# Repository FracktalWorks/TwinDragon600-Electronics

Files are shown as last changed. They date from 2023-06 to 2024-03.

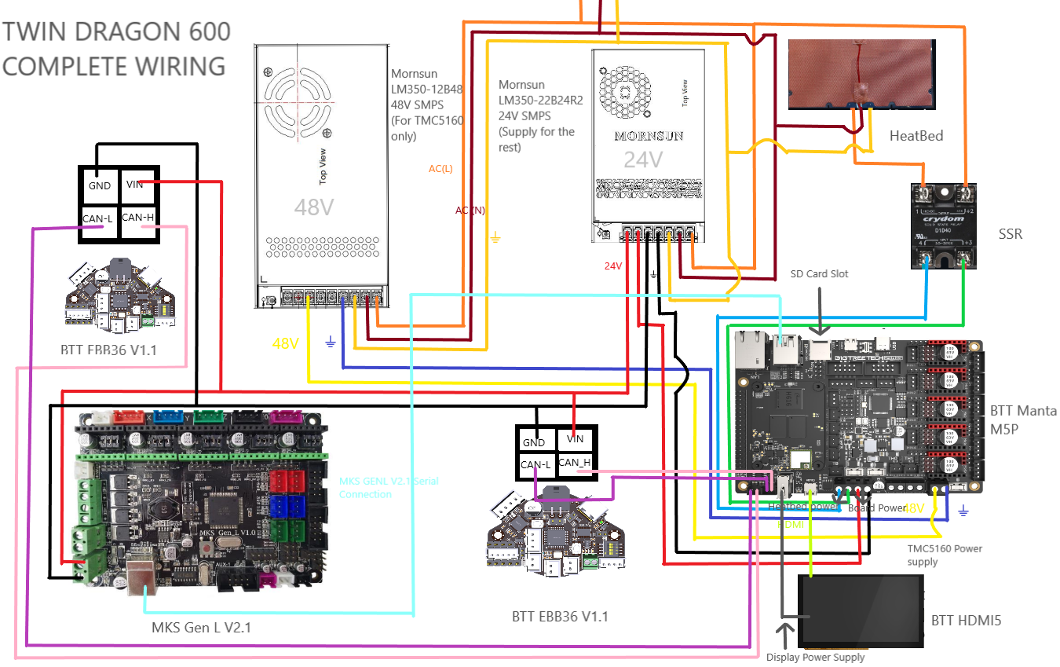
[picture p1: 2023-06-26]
Twin Dragon 600 Wiring.png

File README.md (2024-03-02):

# TwinDragon600-Electronics

### For the Combination of BTT Manta M5P + BTT CB1 + BTT EBB36 + MKS Gen L V2.1

Electronic description, pinout and manuals for the electronics used in Twin Dragon 600

Pin Configurations, jumper selection, CanBus and multi-MCU wiring to BTT CB1 embedded onto BTT Manta M5P for Twin Dragon 600

Components used:
1. BTT Manta M5P - 1
2. BTT CB1 (embed onto BTT Manta M5P) - 1
3. BTT EBB36 Can Module/Toolboard - 2
4. TMC5160 Stepper drivers - 5
5. MKS Gen L V2.1 - 1
6. TMC2209 stepper drivers - 2 (On the MKS GenL) + 2 (Present on the BTT EBB36's)
7. BTT HDMI5 Touch Display

### For the Combination of BTT Manta M8P + BTT CB1 + RP2040 based toolboard

Pin Configurations, jumper selection, CanBus and multi-MCU wiring to BTT CB1 embedded onto BTT Manta M8P for Twin Dragon 600

Components used:
1. BTT Manta M8P - 1
2. BTT CB1 (embed onto BTT Manta M8P) - 1
3. RP2040 based Can Module/Toolboard - 2
4. TMC5160 Stepper drivers - 5
5. TMC2209 stepper drivers - 2 (On the MKS GenL) + 2 (Present on the Toolboards)
6. BTT HDMI5 Touch Display

## Setting up BTT Manta M5P + BTT CB1 + BTT EBB36 + MKS Gen L V2.1

### Initial Preparation

At the Initial stage, when needed to only access the CB1 module with USB power supply, a jumper is to be placed in the slot mentioned as 'VUSB' present between the micro HDMI port and the SOC-SD card slot.


This should not be inserted when the board is supplied with 24V and fully functioning.

### Other Initial preparation and setting up jumpers

#### TMC Driver SPI Mode


The first row are the defined pin for the drivers, which are either high or low when shorted or unshorted to establish different mode of communication. The second row are defined with the SPI modes, with the namings of 'MISO', 'CS', 'SCK' and 'MOSI' when read from left to right. Since we use the TMC5160 driver, it specifically operates only on the SPI mode. Insert the jumpers corresponding to its parallel pins only on the 1st and the 2nd row as shown in the image.

#### Driver Voltage selection


Since the TMC5160 operates only on SPI mode, which is specifically for achieving faster communication and higher speeds, it needs an operating voltage of around 48V. The manta M5P has seperte pins for regular voltage of 24V and high voltage of 48V, that is to be jumped to the common pin of voltage supply to the drivers. We jump the HV pin in the left to the middle pin of supply in order to provide 48V to the drivers, as shown in the image above.

#### Setting up jumper for probe activation


The pin for probe used here is the IND-probe pin on Manta M5P, and the jumper is placed on the two pins beside the probe pins as shown in the image above, to enable 24V supply to the ABL board.

#### Setting up Jumper for CANBUS communication


At the bottom-left corner of the board, a small jumper is to be placed on the pins that mention '120R' depicting the 120 ohms resistance that is applied on the CAN Low and High communication pins. This is a crucial pin for the setting up of the CAN communication of the motherboard and toolboard.

## Setting up of BTT EBB36 CAN module/Toolboard

### Initial preparation


After the motherboard is powered on, the yellow-green LED1 lights will light up, indicating a normal power supply. The VUSB on the right side of the board is the power selection terminal. Only when using USB to supply power to the motherboard or need to supply power through USB, do you need to use the jumper cap to connect VUSB.

#### Setting up Jumper for CANBUS communication


Similar to the BTT Manta M5P, the Support communication via CAN or USB. The terminal resistor 120R of CAN can be selected through a jumper cap, and it reserves a CAN expansion interface.

#### Placing of Heatsink


Place the Heatsink onto the TMC2209 driver chip present on the board which is already embedded onto it as shown in the image above.

## Setting up of MKS GenL V2.1 for side extruder motors

### Setting up jumpers for enabling UART mode


Since we use the TMC2209 for the side extruder motors similar to the main extruder motors, we set the drivers in UART mode

## Wiring and Connections
Twin Dragon 600 Wiring

The overall connections of all the Electrical and Electronic components are present in the image above

### BTT Manta M5P Pin connections
BTT manta M5P pin connections

### EBB36 Pin connections
EBB36 pin connections



The setting up of CANBUS communication in the right angle to avoid confusion

### MKS GenL V2.1 Pin Conections


In the above image, the pin connections of side extruder motors are given, along with additional ports for the extruder filament sensors

## Setting up BTT Manta M8P + BTT CB1 + RP2040 based toolboard

### Initial Preparation

At the Initial stage, when needed to only access the CB1 module with USB power supply, a jumper is to be placed in the slot mentioned as 'VUSB' present behind the Type-C port. After the M8P motherboard is powered on, the D32 red light on the left side of the MCU will light up, indicating that the power supply is normal.



### Other Initial preparation and setting up jumpers

#### TMC Driver SPI Mode



The first row are the defined pin for the drivers, which are either high or low when shorted or unshorted to establish different mode of communication. The second row are defined with the SPI modes, with the namings of 'MISO', 'CS', 'SCK' and 'MOSI' when read from left to right. Since we use the TMC5160 driver, it specifically operates only on the SPI mode. Insert the jumpers corresponding to its parallel pins only on the 1st and the 2nd row as shown in the image.

#### TMC Driver UART Mode



The given set of pin to short is the CS pin that enables only the uart mode.

#### Driver Voltage selection

For High Voltage selection(48V):



Since the TMC5160 operates only on SPI mode, which is specifically for achieving faster communication and higher speeds, it needs an operating voltage of around 48V. The manta M8P has seperte pins for regular voltage of 24V and high voltage of 48V, that is to be jumped to the common pin of voltage supply to the drivers. We jump the HV pin in the left to the middle pin of supply in order to provide 48V to the drivers, as shown in the image above.

For normal Voltage selection (24V):



This voltage selection can be used when using a regular TMC2209 on the UART mode

#### Setting up jumper for probe activation



The pin for probe used here is the IND-probe pin on Manta M8P, and the jumper is placed on the two pins beside the probe pins as shown in the image above, to enable 24V supply to the ABL board.

#### Setting up Jumper for CANBUS communication



At the top of the two CAN pins, a small jumper is to be placed on the pins that mention '120R' depicting the 120 ohms resistance that is applied on the CAN Low and High communication pins. This is a crucial pin for the setting up of the CAN communication of the motherboard and toolboard.

## Setting up of RP2040 based CAN module/Toolboard



After the motherboard is powered on, the green LED light will light up, indicating a normal power supply. The VBUS on the right side of the board is the power selection terminal. Only when using USB to supply power to the motherboard or need to supply power through USB, do you need to use the jumper cap to connect VBUS.

Similar to the BTT Manta M8P, the Support communication via CAN or USB. The terminal resistor 120R of CAN can be selected through a jumper cap, and it reserves a CAN expansion interface.

## Wiring and Connections

Twin Dragon 600 with M8P Wiring

The overall connections of all the Electrical and Electronic components are present in the image above

  ### BTT Manta M8P Pin connections



## Setting up BTT Manta M8P V2.0 + RPi CM4 + RP2040 based toolboard

After powering on the M8P, the LED on the bottom left corner will light up to indicate normal power supply. The VUSB jumper in the center is for selecting power - it should only be shorted when powering the board via USB or supplying power out via USB.



### Other Initial preparation and setting up jumpers

#### TMC Driver SPI Mode



The first row are the defined pin for the drivers, which are either high or low when shorted or unshorted to establish different mode of communication. The second row are defined with the SPI modes, with the namings of 'MISO', 'CS', 'SCK' and 'MOSI' when read from left to right. Since we use the TMC5160 driver, it specifically operates only on the SPI mode. Insert the jumpers corresponding to its parallel pins only on the 1st and the 2nd row as shown in the image.

#### TMC Driver UART Mode



The given set of pin to short is the CS pin that enables only the uart mode.

#### Driver Voltage selection

For High Voltage selection(48V):



Since the TMC5160 operates only on SPI mode, which is specifically for achieving faster communication and higher speeds, it needs an operating voltage of around 48V. The manta M8P has seperte pins for regular voltage of 24V and high voltage of 48V, that is to be jumped to the common pin of voltage supply to the drivers. We jump the HV pin in the left to the middle pin of supply in order to provide 48V to the drivers, as shown in the image above.

For normal Voltage selection (24V):



This voltage selection can be used when using a regular TMC2209 on the UART mode

#### Setting up jumper for probe activation



The pin for probe used here is the IND-probe pin on Manta M8P V2.0, and the jumpers are placed on the two pins beside the probe pins, and other three perpendicular pins to its right, where the top two are to jumped together to activate the probe pin, as shown in the image above, to enable 24V/5V supply to the ABL board. The three columns of the pins starting from the top are 5V, 12V, 24V Respectively.

#### Setting up Jumper for CANBUS communication



At the left of the CAN pin, a small jumper is to be placed on the pins that mention '120R' depicting the 120 ohms resistance that is applied on the CAN Low and High communication pins. This is a crucial pin for the setting up of the CAN communication of the motherboard and toolboard.

## Wiring and Connections

Twin Dragon 600 CM4 M8P V2 0 - Wiring

The overall connections of all the Electrical and Electronic components are present in the image above

### BTT Manta M8P V2.0 Pin connections

Twin Dragon 600 with M8P V2 0 Wiring

## To setup Raspeberry Pi camera Rev 1.3, interfaced with RPi CM4 and BTT Manta M8P/M5P

In order to interface the Pi camera Rev 1.3 with the RPi CM4 and BTT Manta M8P/M5P, flip the board and check for a CSI1 camera slot, which should look like the image below



Instructions to attach the camera in BTT Manta M8P V2.0



Instructions to attach the camera in BTT Manta M5P

1. Now, boot up the board (including CM4), SSH into the CM4 and open the terminal
2. We will have to download a bin file into the boot folder of the CM4, below is the command to enter into the terminal.

`sudo wget https://datasheets.raspberrypi.com/cmio/dt-blob-cam1.bin -O /boot/dt-blob.bin`

If the above command does not work, try the following command:

`sudo wget https://datasheets.raspberrypi.com/cmio/dt-blob-cam1.bin -O /boot/firmware/dt-blob.bin`

3. Now, in the terminal, enter `sudo raspi-config` and select the option '3 Interface Options    Configure connections to peripherals'. Now select the first option 'P1 Camera      Enable/disable connection to the Raspberry Pi Camera'. A pop-up would appear where it asks to enable the camera. Make sure to select <yes> and exit the portal.

4. Now, in the terminal, type in `sudo nano /boot/config.txt` and make sure the settings are enabled

   `start_x=1
   gpu_mem=128`

   Note: make sure `#camera_auto_select=1` is commented out, or else it will not work.

For more clarifications, check out 'Julia TouchUI documentation' for more settings on Pi-camera

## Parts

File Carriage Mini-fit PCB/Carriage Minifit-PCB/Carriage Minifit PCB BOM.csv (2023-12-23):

Qty | Designator | Footprint | Comment | LCSC Part # | Description | Value
1 | J1 | MOLEX_39281063 | 39281063 |  | Conn Wire to Board HDR 6Power POS 4.2mm Solder ST Top Entry Thru-Hole Mini-Fit Jr Bag Check availability | 39281063
1 | X1 | JST-XH-02-PACKAGE-LONG-PAD | JST-XH-02-PIN-LONG-PAD |  | JST XH Connector 2 Pin | JST-XH-02-PIN-LONG-PAD
1 | X2 | TERMINAL-BLOCK-4-PIN-3.5MM-LONG-PAD | TERMINAL-BLOCK-3.5MM-4-PIN-LONG-PAD |  | Terminal Block 3.5mm | TERMINAL-BLOCK-3.5MM-4-PIN-LONG-PAD

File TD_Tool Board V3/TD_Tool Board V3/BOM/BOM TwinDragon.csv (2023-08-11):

Qty | Designator | Footprint | Comment | LCSC part# | Description | Value
1 | J1 | SCREWTERMINAL-3.5MM-2 | CONN_023.5MM |  | Multi connection point. Often used as Generic Header-pin footprint for 0.1 inch spaced/style header connections
2 | R8, R14 | RESC1005X40 | R_CHIP-0402(1005-METRIC) | C25741 | Resistor Fixed - Generic | 100k
22 | C5, C6, C7, C8, C9, C10, C11, C12, C16, C17, C18, C20, C24, C25, C26, C27, C29, C30, C31, C34, C39, C40 | CAPC1005X60 | C_CHIP-0402(1005-METRIC) | C307331 | Capacitor - Generic | 100nF
1 | C33 | PANASONIC_D | 100UF-POLAR-25V-20%(ELEC) | C128464 | 100µF polarized capacitors | 100uF
1 | R6 | RESC1005X40 | R_CHIP-0402(1005-METRIC) | C2933067 | Resistor Fixed - Generic | 105k
4 | R21, R22, R37, R41 | RESC1005X40 | R_CHIP-0402(1005-METRIC) | C25744 | Resistor Fixed - Generic | 10K
1 | C19 | CAPC1608X85 | C_CHIP-0603(1608-METRIC) | C194427 | Capacitor - Generic | 10uF
1 | R16 | RESC1005X40 | R_CHIP-0402(1005-METRIC) | C25079 | Resistor Fixed - Generic | 120R
1 | R9 | RESC1005X40 | R_CHIP-0402(1005-METRIC) | C2974007 | Resistor Fixed - Generic | 13.3k
6 | R3, R12, R23, R24, R25, R40 | RESC1005X40 | R_CHIP-0402(1005-METRIC) | C25543 | Resistor Fixed - Generic | 1K
1 | R2 | RESC1005X40 | R_CHIP-0402(1005-METRIC) | C25086 | Resistor Fixed - Generic | 1R
5 | C3, C4, C13, C14, C15 | CAPC1005X60 | C_CHIP-0402(1005-METRIC) | C52923 | Capacitor - Generic | 1uF
2 | R35, R36 | RESC1005X40 | R_CHIP-0402(1005-METRIC) | C425373 | Resistor Fixed - Generic | 2.37K
1 | R1 | RESC1005X40 | R_CHIP-0402(1005-METRIC) | C25087 | Resistor Fixed - Generic | 200R
4 | R30, R45, R47, R49 | RESC1005X40 | R_CHIP-0402(1005-METRIC) | C25765 | Resistor Fixed - Generic | 20K
2 | R26, R27 | RESC1005X40 | R_CHIP-0402(1005-METRIC) | C705474 | Resistor Fixed - Generic | 220mΩ
1 | C28 | CAPC1005X60 | C_CHIP-0402(1005-METRIC) | C1532 | Capacitor - Generic | 22nF
3 | C21, C22, C38 | CAPC2012X110 | C_CHIP-0805(2012-METRIC) | C338080 | Capacitor - Generic | 22uF
6 | R10, R11, R31, R44, R46, R48 | RESC1005X40 | R_CHIP-0402(1005-METRIC) | C31439 | Resistor Fixed - Generic | 27.4R
1 | P2 | SOT23-5 | V_REG_AP2112K-3.3V | C51118 | AP2112 - 600mA CMOS LDO Regulator w/ Enable | 3.3V
2 | C1, C2 | CAPC1005X60 | C_CHIP-0402(1005-METRIC) | C1570 | Capacitor - Generic | 30pF
1 | R34 | RESC1005X40 | R_CHIP-0402(1005-METRIC) | C227106 | Resistor Fixed - Generic | 4.12K
5 | R17, R18, R19, R20, R33 | RESC1005X40 | R_CHIP-0402(1005-METRIC) | C304616 | Resistor Fixed - Generic | 4.7K
5 | C32, C42, C43, C44, C45 | CAPC1608X85 | C_CHIP-0603(1608-METRIC) | C162274 | Capacitor - Generic | 4.7uF
3 | R7, R15, R28 | RESC1005X40 | R_CHIP-0402(1005-METRIC) | C25120 | Resistor Fixed - Generic | 49.9R
1 | R5 | RESC1005X40 | R_CHIP-0402(1005-METRIC) | C3037035 | Resistor Fixed - Generic | 511k
1 | C23 | CAPC1005X60 | C_CHIP-0402(1005-METRIC) | C37809 | Capacitor - Generic | 75pF
1 | L2 | ACM2012_TDK | ACM2012-201-2P-T002ACM2012_TDK | C3029258 |  | ACM2012
1 | U5 | ADXL345_LGA14 | ADXL345BCCZ-RL | C9667 | Digital Accelerometer | ADXL345
1 | L1 | SMDRI74-680MT | ASPI-0630HI-100M-T157X7X4 | C3000391 | Inductor Power Molded Wirewound 10uH 20% 3A 105mOhm DCR T/R | ASPI-0630HI-100M-T157X7X4
2 | BOOT, RST | B3U-1000P(M)-B | B3U-X000B3U-1000P(M)-B1000P(M)-B | C231329 | Ultra-small Tactile Switch | B3U-1000P(M)-B
4 | D4, D6, D7, D8 | SOT23 | BAT54S | C47546 |  | BAT54S
3 | M2, M3, M4 | SOT23 | NMOSFET_BSS123_SOT23-GSD | C19019 | N-Channel MOSFET - Popular parts | CJ3400
1 | X1 | CRYSTAL_3225 | CRYSTAL_TAXM12M4RLBDDT2T_3225 | C133334 |  | CRYSTAL_TAXM12M4RLBDDT2T_3225
1 | R13 | RESC1005X40 | R_CHIP-0402(1005-METRIC) | NO-FIT | Resistor Fixed - Generic | DO NOT FIT (10K)
3 | FD4, FD5, FD6 | FIDUCIAL_1MM | FIDUCIAL |  | For use by pick and place machines to calibrate the vision/machine, 1mm | FIDUCIAL
1 | F1 | FUSC1608X60N | FUSE_CHIP-0603(1608-METRIC) | C261937 | Fuse - Generic | FUSE_CHIP-0603(1608-METRIC)
1 | J3 | CON_430450400_MOL | 430450400CON_430450400_MOL |  |  | JST-MICROFIT
1 | C_FAN2 | JST-XH-02-PACKAGE-LONG-PAD | JST-XH-02-PIN-LONG-PAD |  | JST XH Connector 2 Pin | JST-XH
5 | CANBUS, C_FAN, ENDSTOP, H_FAN, M_FAN | JST-XH-02-PACKAGE-LONG-PAD | JST-XH-02-PIN-LONG-PAD |  | JST XH Connector 2 Pin | JST-XH-02-PIN-LONG-PAD
1 | EXTRUDER | JST-XH-04-PACKAGE-LONG-PAD | JST-XH-04-PIN-LONG-PAD |  | JST XH Connector 2 Pin | JST-XH-04-PIN-LONG-PAD
1 | D3 | LEDC1608X35N_FLAT-G | CHIP-FLAT-G_0603-0.35MM | C72043 |  | LED_G
1 | D9 | LED3MM | LED3MM | C72043 | LED | LED_G
1 | D1 | SODFL3718X115 | SCHOTTKY_MBR0520LT1GDO-219 | C23848 | Schottky Diode - Popular parts | MBR0520LT1G
1 | M1 | NMOSFET_WSD3066DN33 | NMOSFET_WSD3066DN33 | C148386 |  | NMOSFET_WSD3066DN33
1 | R4 | RESC1005X40 | R_CHIP-0402(1005-METRIC) | NO-FIT | Resistor Fixed - Generic | NO-FIT
1 | U1 | IC57_RP2040-L | RP2040IC57_RP2040-L | C2040 |  | RP2040
1 | U3 | D8-L | SN65HVD1050DRD8-L | C14019 |  | SN65HVD
1 | U6 | DBV5-L | SN74LVC1G17DBVRDBV5-L | C7836 |  | SN74L
1 | SJ2 | SJ_2S-NO | SOLDERJUMPERNO |  | Solder Jumper | SOLDERJUMPERNO
2 | SJ1, SJ3 | SJ_2S-TRACE | SOLDERJUMPERTRACE |  | Solder Jumper | SOLDERJUMPERTRACE
2 | IO1, IO2 | PAD.03X.03 | TEST-POINT3 |  | SparkFun Test Points | TEST-POINT3
10 | 3.3V, 5V, 24V, A1, A2, B1, B2, GND, HE0, TH0 | PAD.03X.04 | TEST-POINT3X4 |  | SparkFun Test Points | TEST-POINT3X4
1 | U7 | QFN28_5X5_3X8_EPAD_TRI | TMC2209-LA-TQFN28_5X5_3X8_EPAD_TRI | C2150710 |  | TMC2209
1 | P1 | SOT-23-6 | TPS54202_BUCKCONV | C191884 |  | TPS54202_BUCKCONV
1 | USB | CONN12_016JA1R1500_JAE | USB-C(DX07S016JA1R1500) | C709357 |  | USB-C(DX07S016JA1R1500)
1 | D2 | SOT-666_STM-L | USBLC6-2P6SOT-666_STM-L | C2827693 |  | USBLC6-2P6SOT-666_STM-L
1 | U2 | SOIC_128JVSIQ_WIN-L | W25Q128JVSIQSOIC_128JVSIQ_WIN-L | C97521 |  | W25Q128

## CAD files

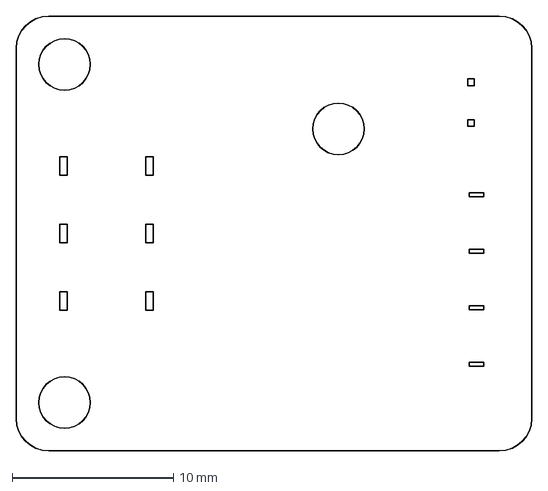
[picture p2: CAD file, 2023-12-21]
Carriage Mini-fit PCB/TD Carriage MINIFIT board.dxf
32.0 x 27.0 mm

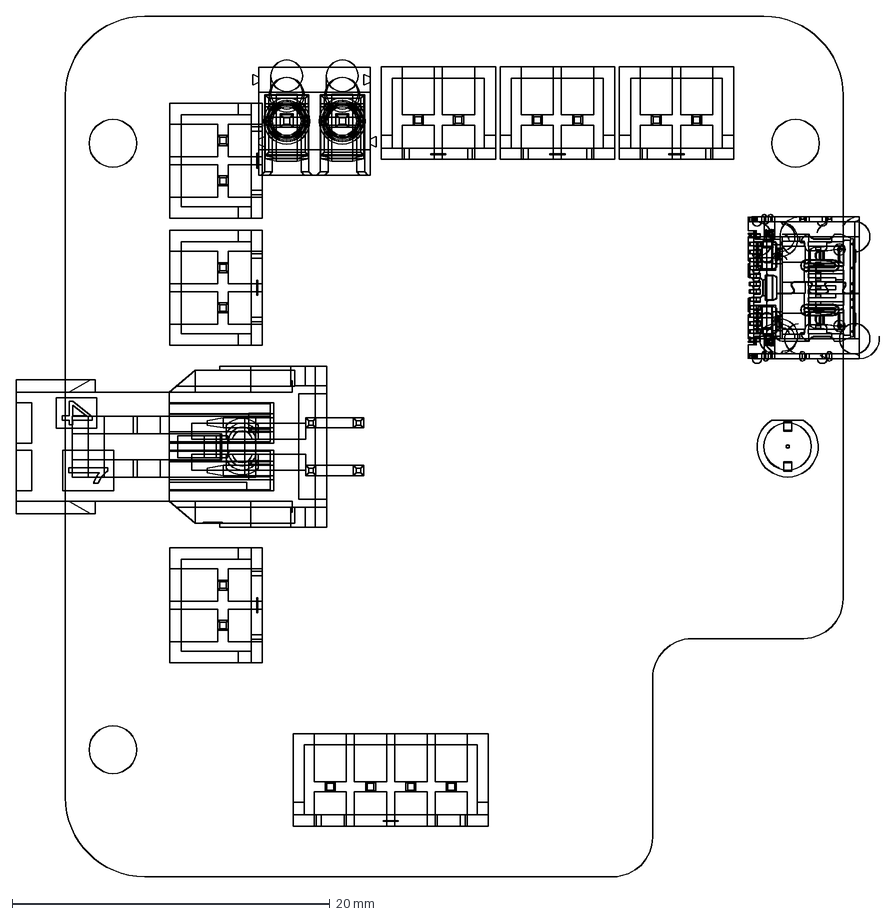
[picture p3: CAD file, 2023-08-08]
TD_Tool Board V3/PCB V2.1.dxf
54.4 x 54.2 mm

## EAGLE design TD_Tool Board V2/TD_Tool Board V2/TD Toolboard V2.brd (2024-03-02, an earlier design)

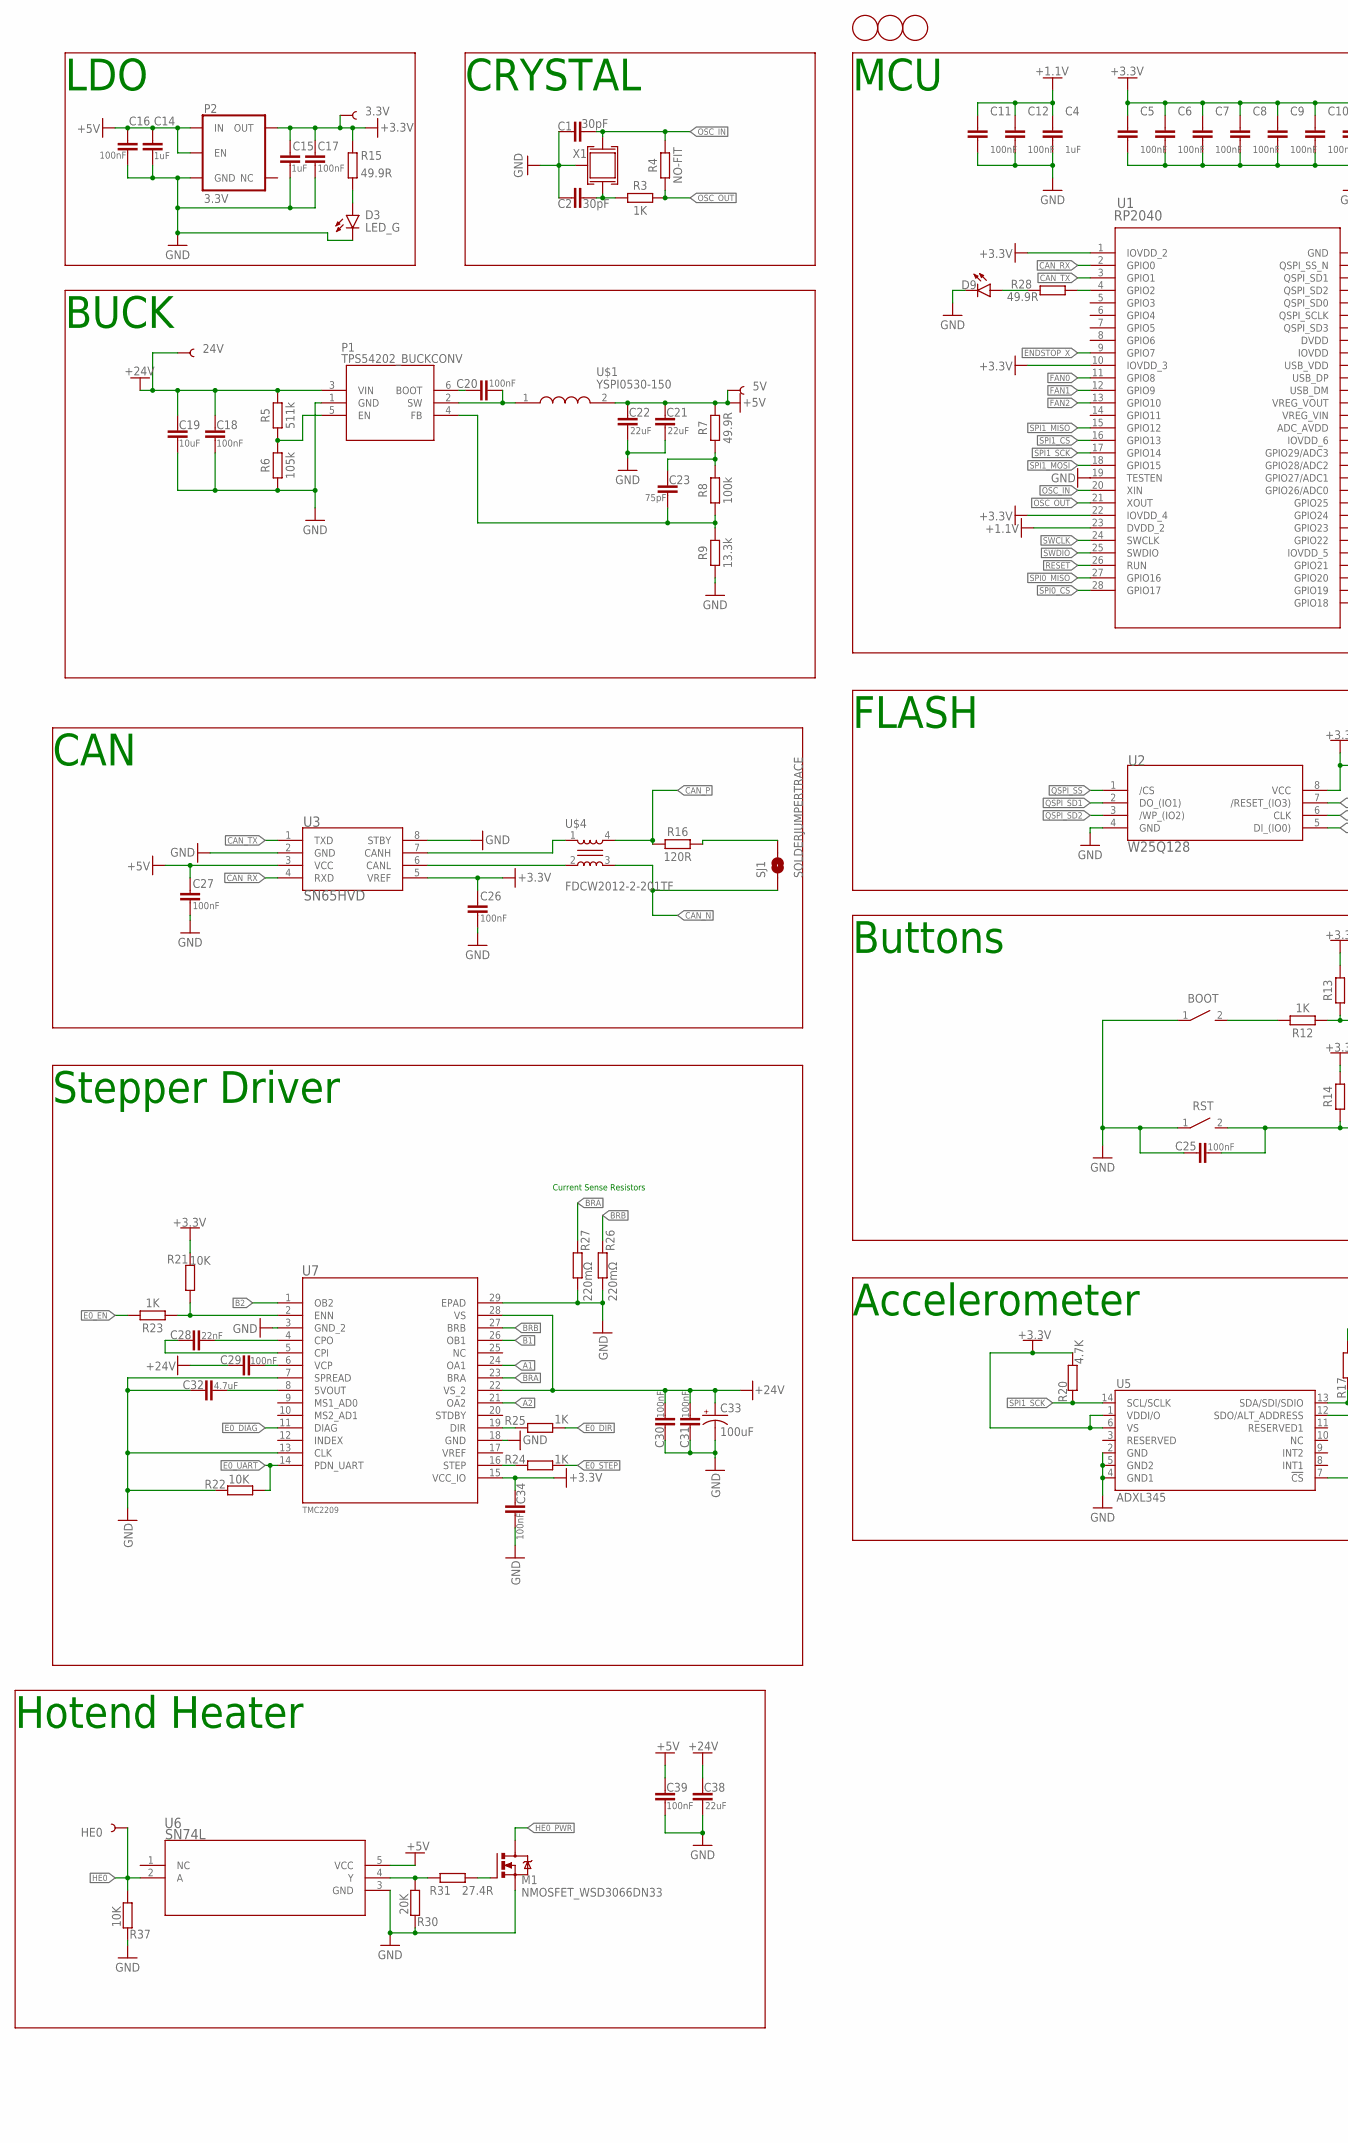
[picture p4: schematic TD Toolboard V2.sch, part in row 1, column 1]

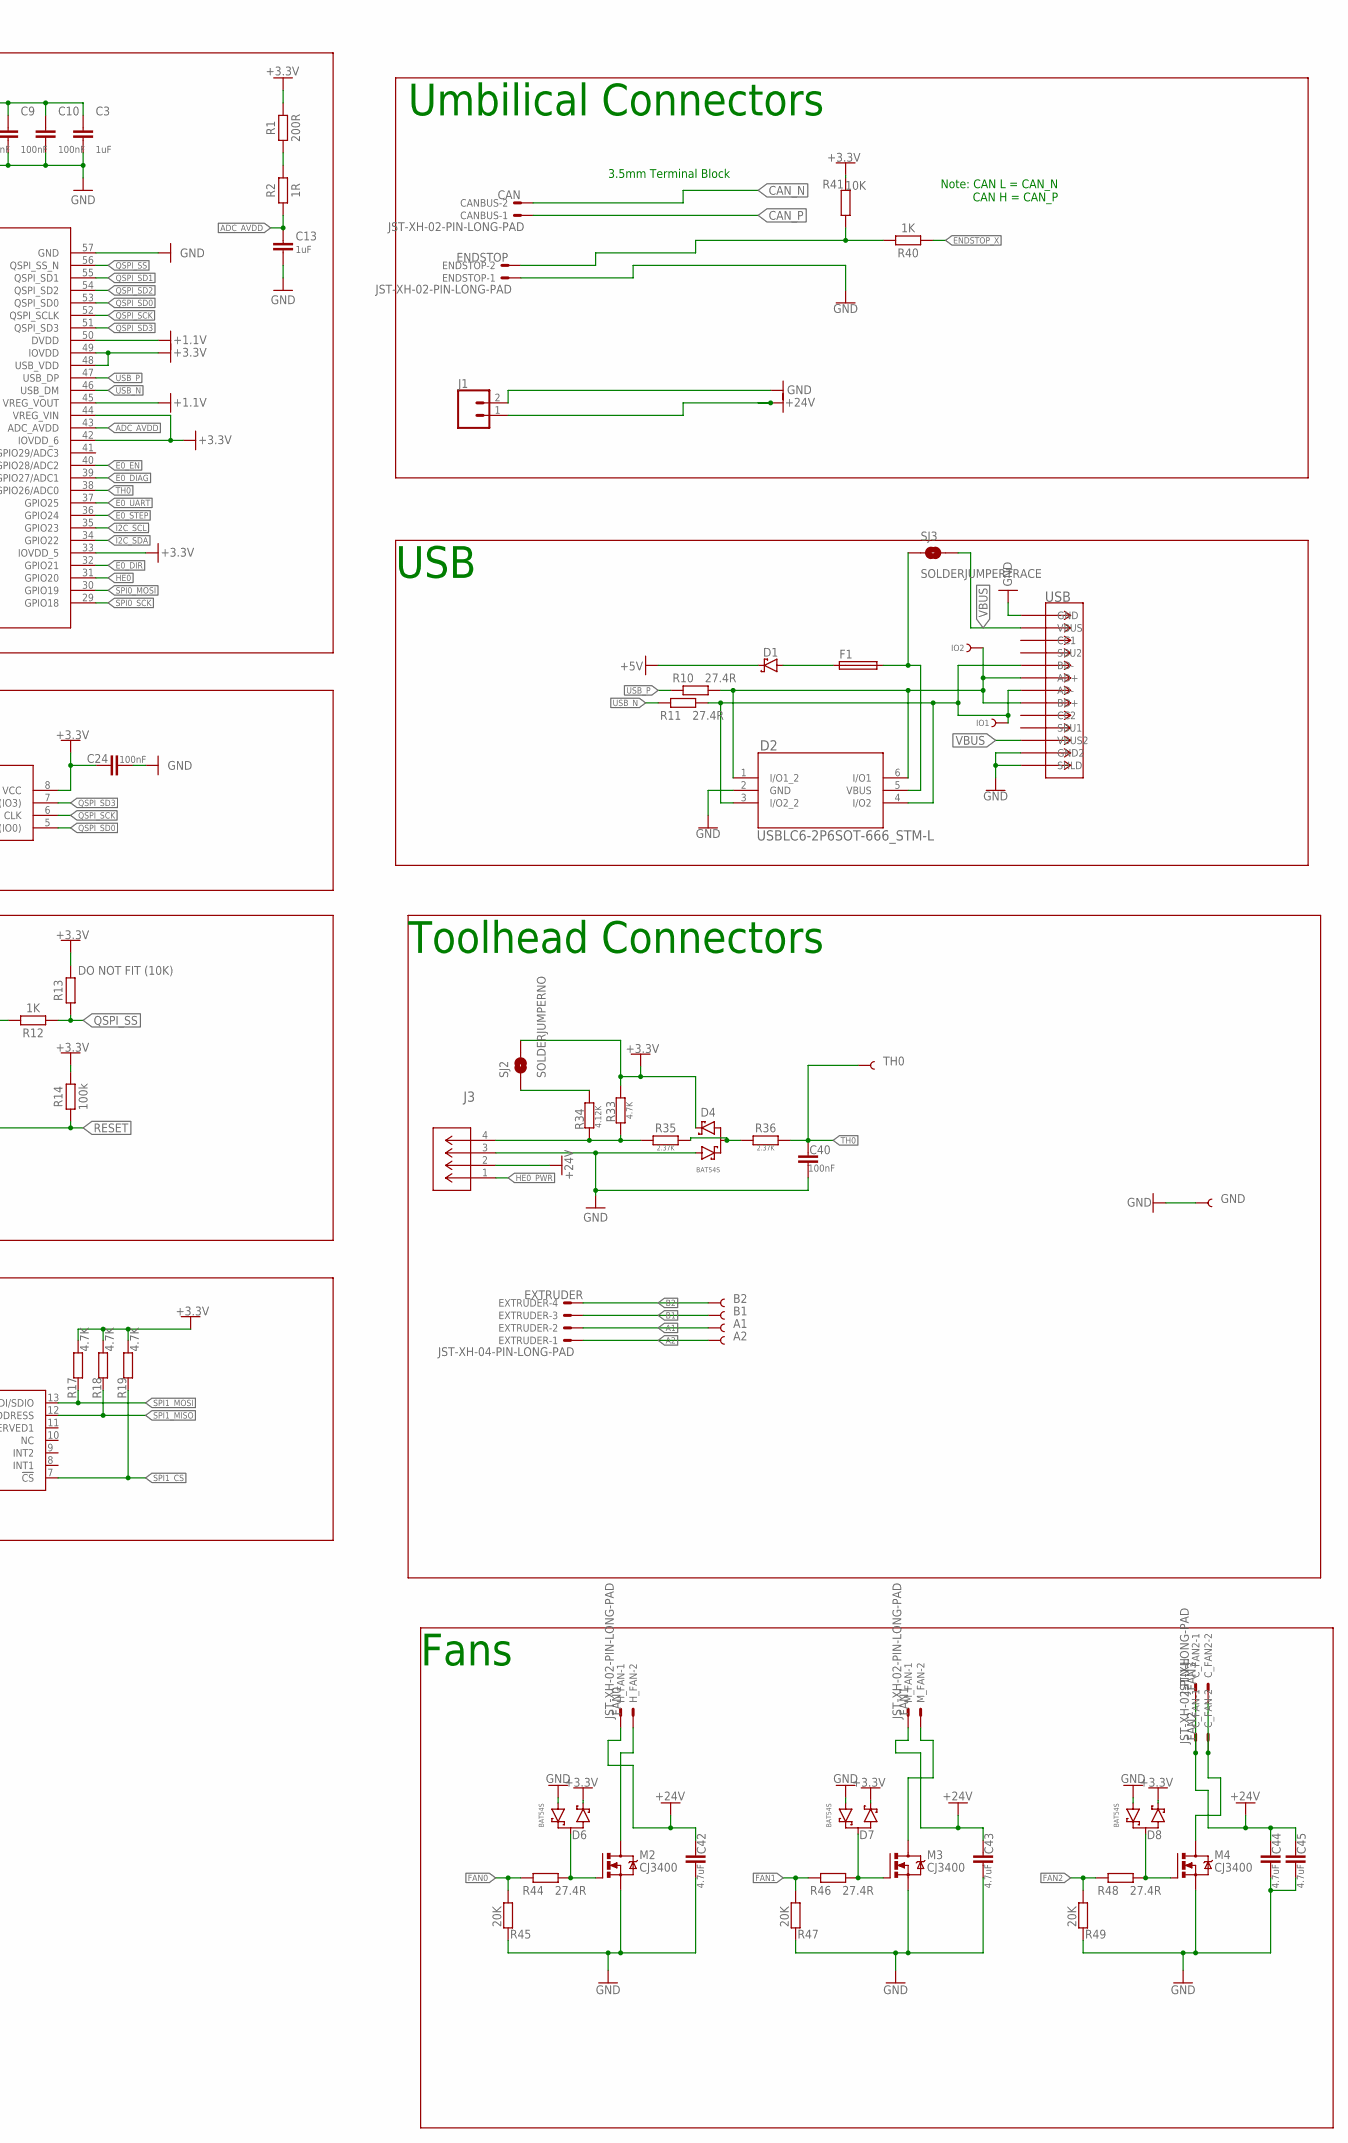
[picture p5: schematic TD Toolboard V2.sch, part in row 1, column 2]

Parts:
3.3V, 5V, 24V: TEST-POINT3X4; PAD.03X.04
A1, A2: TEST-POINT3X4; PAD.03X.04
B1, B2: TEST-POINT3X4; PAD.03X.04
BOOT: B3U-1000P(M)-B; LCSCPN# C231329
C1, C2: 30pF; CAPC1005X60; LCSCPN# C1570
C3, C4, C13, C14, C15: 1uF; CAPC1005X60; LCSCPN# C52923
C5, C6, C7, C8, C9, C10, C11, C12, C16, C17, C18, C20, C24, C25, C26, C27, C29, C30, C31, C34, C39, C40: 100nF; CAPC1005X60; LCSCPN# C307331
C19: 10uF; CAPC1608X85; LCSCPN# C194427
C21, C22, C38: 22uF; CAPC2012X110; LCSCPN# C338080
C23: 75pF; CAPC1005X60; LCSCPN# C37809
C28: 22nF; CAPC1005X60; LCSCPN# C1532
C32, C42, C43, C44, C45: 4.7uF; CAPC1608X85; LCSCPN# C162274
C33: 100uF; PANASONIC_D; LCSCPN# C128464
CANBUS: JST-XH-02-PIN-LONG-PAD; JST-XH-02-PACKAGE-LONG-PAD
C_FAN: JST-XH-02-PIN-LONG-PAD; JST-XH-02-PACKAGE-LONG-PAD
C_FAN2: JST-XH; JST-XH-02-PACKAGE-LONG-PAD
D1: MBR0520LT1G; SODFL3718X115
D2: USBLC6-2P6SOT-666_STM-L; SOT-666_STM-L; LCSCPN# C2827693
D3: LED_G; LEDC1608X35N_FLAT-G; LCSCPN# C72043
D4, D6, D7, D8: BAT54S; SOT23; LCSCPN# C47546
D9: LED_G; LED3MM; LCSCPN# C72043
ENDSTOP: JST-XH-02-PIN-LONG-PAD; JST-XH-02-PACKAGE-LONG-PAD
EXTRUDER: JST-XH-04-PIN-LONG-PAD; JST-XH-04-PACKAGE-LONG-PAD
F1: FUSE_CHIP-0603(1608-METRIC); FUSC1608X60N; LCSCPN# C261937
FD4, FD5, FD6: FIDUCIAL; FIDUCIAL_1MM
GND: TEST-POINT3X4; PAD.03X.04
HE0: TEST-POINT3X4; PAD.03X.04
H_FAN: JST-XH-02-PIN-LONG-PAD; JST-XH-02-PACKAGE-LONG-PAD
IO1, IO2: TEST-POINT3; PAD.03X.03
J1: CONN_023.5MM; SCREWTERMINAL-3.5MM-2
J3: JST-MICROFIT; CON_430450400_MOL
M1: NMOSFET_WSD3066DN33; LCSCPN# C148386
M2, M3, M4: CJ3400; SOT23; LCSCPN# C19019
M_FAN: JST-XH-02-PIN-LONG-PAD; JST-XH-02-PACKAGE-LONG-PAD
P1: TPS54202_BUCKCONV; SOT-23-6; LCSCPN# C191884
P2: 3.3V; SOT23-5; LCSCPN# C51118
R1: 200R; RESC1005X40; LCSCPN# C25087
R2: 1R; RESC1005X40; LCSCPN# C25086
R3, R12, R23, R24, R25, R40: 1K; RESC1005X40; LCSCPN# C25543
R4: NO-FIT; RESC1005X40; LCSCPN# NO-FIT
R5: 511k; RESC1005X40; LCSCPN# C3037035
R6: 105k; RESC1005X40; LCSCPN# C2933067
R7, R15, R28: 49.9R; RESC1005X40; LCSCPN# C25120
R8, R14: 100k; RESC1005X40; LCSCPN# C25741
R9: 13.3k; RESC1005X40; LCSCPN# C2974007
R10, R11, R31, R44, R46, R48: 27.4R; RESC1005X40; LCSCPN# C31439
R13: DO NOT FIT (10K); RESC1005X40; LCSCPN# NO-FIT
R16: 120R; RESC1005X40; LCSCPN# C25079
R17, R18, R19, R20, R33: 4.7K; RESC1005X40; LCSCPN# C304616
R21, R22, R37, R41: 10K; RESC1005X40; LCSCPN# C25744
R26, R27: 220mΩ; RESC1005X40; LCSCPN# C705474
R30, R45, R47, R49: 20K; RESC1005X40; LCSCPN# C25765
R34: 4.12K; RESC1005X40; LCSCPN# C227106
R35, R36: 2.37K; RESC1005X40; LCSCPN# C425373
RST: B3U-1000P(M)-B; LCSCPN# C231329
SJ1, SJ3: SOLDERJUMPERTRACE; SJ_2S-TRACE
SJ2: SOLDERJUMPERNO; SJ_2S-NO
TH0: TEST-POINT3X4; PAD.03X.04
U1: RP2040; IC57_RP2040-L; LCSCPN# C2040
U2: W25Q128; SOIC_128JVSIQ_WIN-L; LCSCPN# C97521
U3: SN65HVD; D8-L; LCSCPN# C14019
U5: ADXL345; ADXL345_LGA14; LCSCPN# C9667
U6: SN74L; DBV5-L; LCSCPN# C7836
U7: TMC2209; QFN28_5X5_3X8_EPAD_TRI; LCSCPN# C2150710
U$1: YSPI0530-150
U$4: FDCW2012-2-201TF
USB: USB-C(KH-TYPE-C-16P); CONN12_KH-TYPE-C-16P; LCSCPN# C709357
X1: CRYSTAL_TAXM12M4RLBDDT2T_3225; CRYSTAL_3225; LCSCPN# C133334

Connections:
+1.1V: C4.1, C11.1, C12.1, U1.23 (DVDD_2), U1.45 (VREG_VOUT), U1.50 (DVDD)
+3.3V: 3.3V.P$1, C3.1, C5.1, C6.1, C7.1, C8.1, C9.1, C10.1, C15.1, C17.1, C24.1, C26.1, C34.1, D4.2, D6.2, D7.2, D8.2, P2.5 (OUT), R1.2, R13.2, R14.2, R15.2, R17.2, R18.2, R19.2, R20.2, R21.1, R33.2, R41.1, SJ2.2, U1.1 (IOVDD_2), U1.10 (IOVDD_3), U1.22 (IOVDD_4), U1.33 (IOVDD_5), U1.42 (IOVDD_6), U1.44 (VREG_VIN), U1.48 (USB_VDD), U1.49 (IOVDD), U2.8 (VCC), U3.5 (VREF), U5.1 (VDDI/O), U5.6 (VS), U7.15 (VCC_IO)
+5V: 5V.P$1, C14.1, C16.1, C21.1, C22.1, C27.1, C39.1, D1.1 (C), P2.1 (IN), P2.3 (EN), R7.2, U3.3 (VCC), U6.5 (VCC), U$1.2
+24V: 24V.P$1, C18.1, C19.1, C29.1, C30.2, C31.2, C33.+, C38.1, C42.1, C43.1, C44.1, C45.1, C_FAN.1, C_FAN2.1, H_FAN.1, J1.1, J3.2, M_FAN.1, P1.3 (VIN), R5.2, U7.22 (VS_2), U7.28 (VS)
A1: A1.P$1, EXTRUDER.2, U7.24 (OA1)
A2: A2.P$1, EXTRUDER.1, U7.21 (OA2)
ADC_AVDD: C13.1, R2.1, U1.43 (ADC_AVDD)
ADC_R: R1.1, R2.2
B1: B1.P$1, EXTRUDER.3, U7.26 (OB1)
B2: B2.P$1, EXTRUDER.4, U7.1 (OB2)
BCBOOT: C20.1, P1.6 (BOOT)
BRA: R27.2, U7.23 (BRA)
BRB: R26.2, U7.27 (BRB)
CAN1_N: U3.6 (CANL), U$4.2
CAN1_P: U3.7 (CANH), U$4.1
CAN_N: CANBUS.2, SJ1.1, U$4.3
CAN_P: CANBUS.1, R16.1, U$4.4
CAN_RX: U1.2 (GPIO0), U3.4 (RXD)
CAN_TX: U1.3 (GPIO1), U3.1 (TXD)
CNT: R16.2, SJ1.2
DIR: R25.2, U7.19 (DIR)
E0_DIAG: U1.39 (GPIO27/ADC1), U7.11 (DIAG)
E0_DIR: R25.1, U1.32 (GPIO21)
E0_EN: R23.2, U1.40 (GPIO28/ADC2)
E0_STEP: R24.1, U1.36 (GPIO24)
E0_UART: R22.2, U1.37 (GPIO25), U7.14 (PDN_UART)
ENDSTOP_X: R40.1, U1.9 (GPIO7)
EX: ENDSTOP.2, R40.2, R41.2
FAN0: R44.2, R45.2, U1.11 (GPIO8)
FAN0G: D6.3, M2.1 (G), R44.1
FAN1: R46.2, R47.2, U1.12 (GPIO9)
FAN1G: D7.3, M3.1 (G), R46.1
FAN2: R48.2, R49.2, U1.13 (GPIO10)
FAN2G: D8.3, M4.1 (G), R48.1
GND: BOOT.1, C1.2, C2.1, C3.2, C4.2, C5.2, C6.2, C7.2, C8.2, C9.2, C10.2, C11.2, C12.2, C13.2, C14.2, C15.2, C16.2, C17.2, C18.2, C19.2, C21.2, C22.2, C24.2, C25.1, C26.2, C27.2, C30.1, C31.1, C32.1, C33.-, C34.2, C38.2, C39.2, C40.2, C42.2, C43.2, C44.2, C45.2, D2.2 (GND), D3.C, D4.1, D6.1, D7.1, D8.1, D9.K (C), ENDSTOP.1, GND.P$1, J1.2, J3.3, M1.P$1 (S), M1.P$2 (S), M1.P$3 (S), M2.2 (S), M3.2 (S), M4.2 (S), P1.1 (GND), P2.2 (GND), R6.1, R9.1, R22.1, R26.1, R27.1, R30.1, R37.1, R45.1, R47.1, R49.1, RST.1, U1.19 (TESTEN), U1.57 (GND), U2.4 (GND), U3.2 (GND), U3.8 (STBY), U5.2 (GND), U5.4 (GND1), U5.5 (GND2), U6.3 (GND), U7.3 (GND_2), U7.7 (SPREAD), U7.13 (CLK), U7.18 (GND), U7.29 (EPAD), USB.1 (GND), USB.12 (GND2), USB.13 (SHLD), USB.14 (SHLD), USB.15 (SHLD), USB.16 (SHLD), USB.18 (SHLD), USB.19 (SHLD), USB.20 (SHLD), USB.21 (SHLD), USB.24 (SHLD), USB.25 (SHLD), USB.26 (SHLD), USB.27 (SHLD), USB.28 (SHLD), USB.29 (SHLD), USB.37 (SHLD), USB.39 (SHLD), USB.41 (SHLD), USB.43 (SHLD), X1.P$2 (GND), X1.P$4 (GND)
GPIOLED: D9.A, R28.1
HE0: HE0.P$1, R37.2, U1.31 (GPIO20), U6.2 (A)
HE0A: R30.2, R31.2, U6.4 (Y)
HE0B: M1.P$4 (G), R31.1
HE0_PWR: J3.1, M1.P$5 (D), M1.P$6 (D), M1.P$7 (D), M1.P$8 (D), M1.P$9 (D)
I2C_SCL: U1.35 (GPIO23)
I2C_SDA: U1.34 (GPIO22)
LDOLED: D3.A, R15.1
LED: R28.2, U1.4 (GPIO2)
unnamed: H_FAN.2, M2.3 (D)
unnamed: M3.3 (D), M_FAN.2
unnamed: C_FAN.2, C_FAN2.2, M4.3 (D)
OSC_IN: C1.1, R4.2, U1.20 (XIN), X1.P$1 (P1)
OSC_OUT: R3.2, R4.1, U1.21 (XOUT)
QSPI_SCK: U1.52 (QSPI_SCLK), U2.6 (CLK)
QSPI_SD0: U1.53 (QSPI_SD0), U2.5 (DI_(IO0))
QSPI_SD1: U1.55 (QSPI_SD1), U2.2 (DO_(IO1))
QSPI_SD2: U1.54 (QSPI_SD2), U2.3 (/WP_(IO2))
QSPI_SD3: U1.51 (QSPI_SD3), U2.7 (/RESET_(IO3))
QSPI_SS: R12.1, R13.1, U1.56 (QSPI_SS_N), U2.1 (/CS)
RESET: C25.2, R14.1, RST.2, U1.26 (RUN)
SPI0_CS: U1.28 (GPIO17)
SPI0_MISO: U1.27 (GPIO16)
SPI0_MOSI: U1.30 (GPIO19)
SPI0_SCK: U1.29 (GPIO18)
SPI1_CS: R19.1, U1.16 (GPIO13), U5.7 (!CS)
SPI1_MISO: R18.1, U1.15 (GPIO12), U5.12 (SDO/ALT_ADDRESS)
SPI1_MOSI: R17.1, U1.18 (GPIO15), U5.13 (SDA/SDI/SDIO)
SPI1_SCK: R20.1, U1.17 (GPIO14), U5.14 (SCL/SCLK)
STEP: R24.2, U7.16 (STEP)
SWB: BOOT.2, R12.2
SWCLK: U1.24 (SWCLK)
SWDIO: U1.25 (SWDIO)
TH0: C40.1, R36.2, TH0.P$1, U1.38 (GPIO26/ADC0)
TH0A: J3.4, R33.1, R34.1, R35.1
TH0B: D4.3, R35.2, R36.1
TH0C: R34.2, SJ2.1
TMC5V: C32.2, U7.8 (5VOUT)
TMCCPI: C28.1, U7.5 (CPI)
TMCCPO: C28.2, U7.4 (CPO)
TMCENN: R21.2, R23.1, U7.2 (ENN)
TMCVCP: C29.2, U7.6 (VCP)
USB1_N: D2.3 (I/O2_2), D2.4 (I/O2), IO1.P$1, R11.1, USB.5 (BD-), USB.7 (AD-)
USB1_P: D2.1 (I/O1_2), D2.6 (I/O1), IO2.P$1, R10.1, USB.6 (AD+), USB.8 (BD+)
USB_N: R11.2, U1.46 (USB_DM)
USB_P: R10.2, U1.47 (USB_DP)
VBUS: SJ3.2, USB.2 (VBUS), USB.11 (VBUS2)
VBUS1: D2.5 (VBUS), F1.2, SJ3.1
VBUS3: D1.2 (A), F1.1
VRC: C23.1, R7.1, R8.2
VREGEN: P1.5 (EN), R5.1, R6.2
VREGFB: C23.2, P1.4 (FB), R8.1, R9.2
VREGO: C20.2, P1.2 (SW), U$1.1
XR: C2.2, R3.1, X1.P$3 (P2)

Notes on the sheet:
LDO
BUCK
CRYSTAL
MCU
FLASH
Buttons
Accelerometer
CAN
Stepper Driver
Current Sense Resistors
Hotend Heater
Umbilical Connectors
Note: CAN L = CAN_N CAN H = CAN_P
3.5mm Terminal Block
USB
Toolhead Connectors
Fans

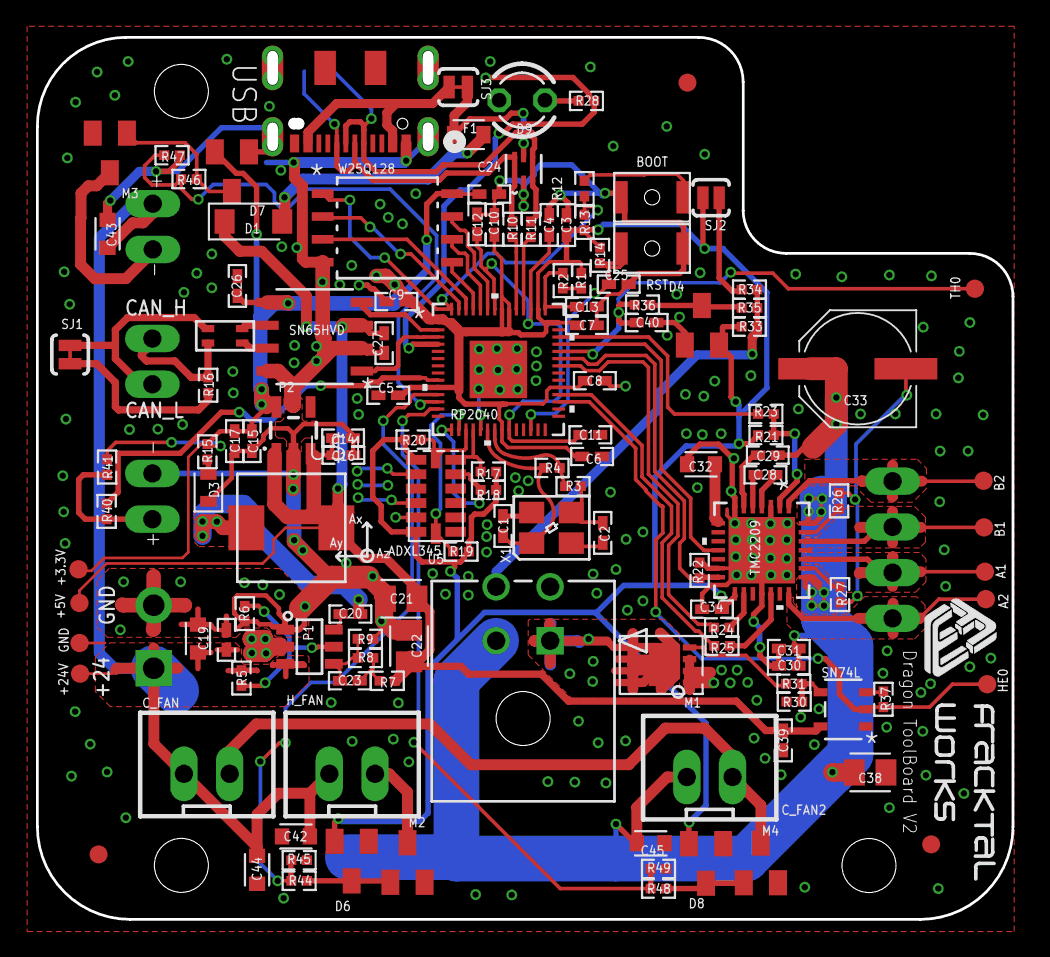
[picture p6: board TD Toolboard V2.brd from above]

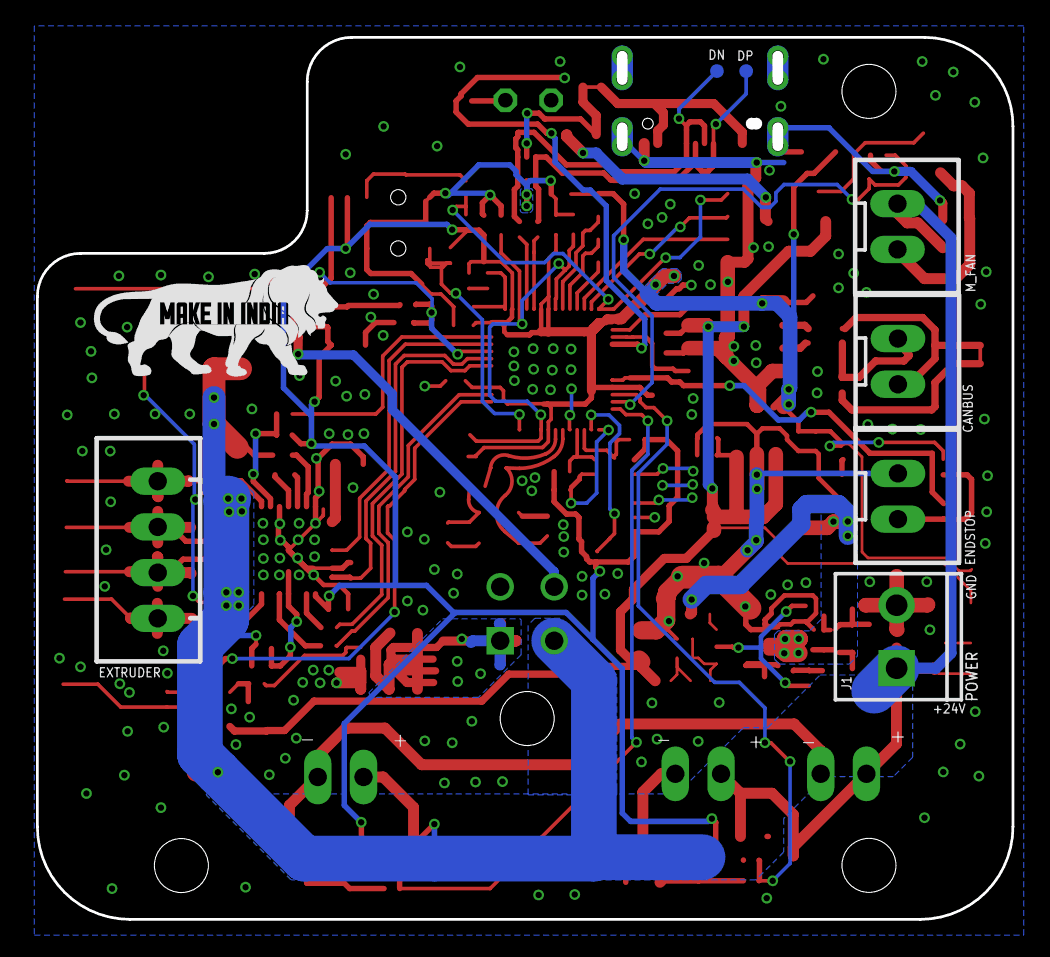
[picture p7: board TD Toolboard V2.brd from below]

Board: 2 copper layers, 54.2 x 49.0 mm, 140 parts (8 on the bottom side), 81 nets.

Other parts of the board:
U$2: MAKEININDIA
U$3: FWLOGO_SMALL

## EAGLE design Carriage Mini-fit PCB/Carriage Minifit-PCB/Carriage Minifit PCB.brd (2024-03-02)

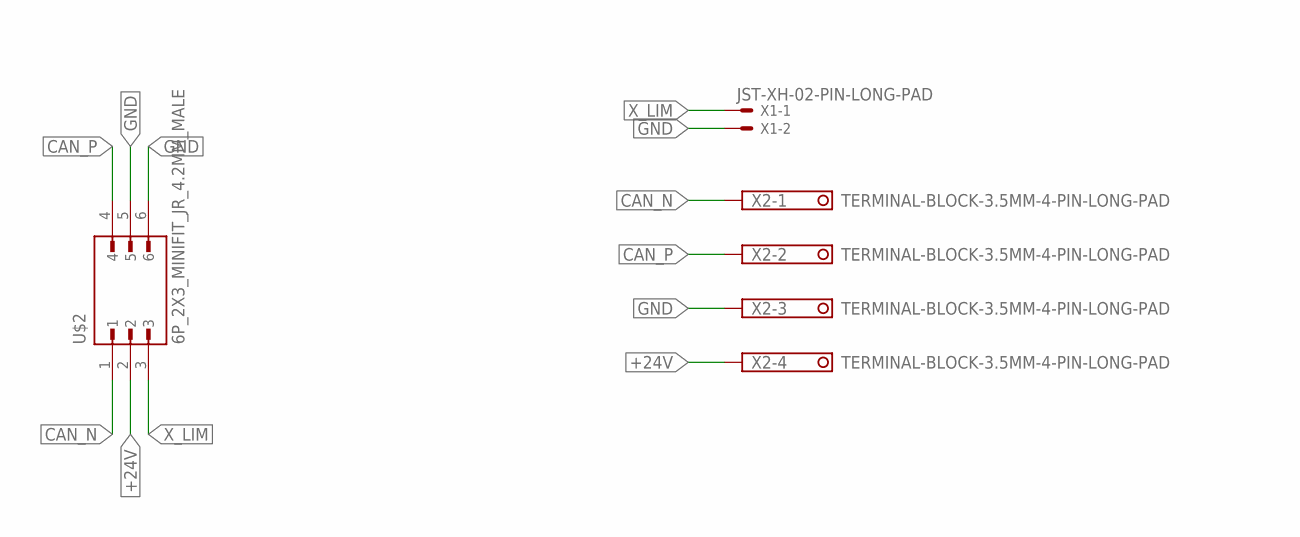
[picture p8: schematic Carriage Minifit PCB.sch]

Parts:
U$2: 6P_2X3_MINIFIT_JR_4.2MM_MALE
X1: JST-XH-02-PIN-LONG-PAD; JST-XH-02-PACKAGE-LONG-PAD
X2: TERMINAL-BLOCK-3.5MM-4-PIN-LONG-PAD; TERMINAL-BLOCK-4-PIN-3.5MM-LONG-PAD

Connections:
+24V: U$2.2, X2.4
CAN_N: U$2.1, X2.1
CAN_P: U$2.4, X2.2
GND: U$2.5, U$2.6, X1.2, X2.3
X_LIM: U$2.3, X1.1

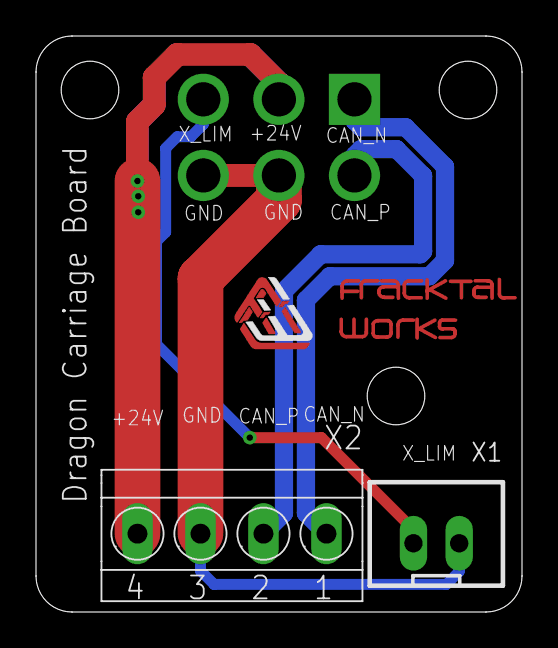
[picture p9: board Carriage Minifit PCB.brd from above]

Board: 2 copper layers, 27.0 x 32.0 mm, 4 parts (1 on the bottom side), 5 nets.

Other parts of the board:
U$1: FWLOGO_SMALL_FOOTPRINT; FWLOGO_SMALL

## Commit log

2023-06-26 Added manuals and wiring diagram
2023-06-27 Update README.md
    Pin connections, description and initial setup of electronics has been updated with images
2023-07-24 Update README.md
    Added pin diagrams and circuits related to Manta M8P and RP2040 toolboard
2023-07-31 added toolboard schematic
    [CAN_new_design.brd, CAN_new_design.sch]
2023-08-04 Added eagle files for current progress in toolboard
    [CAN_new_design.brd, CAN_new_design.sch, CAN_toolboard_redesign.brd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]
2023-08-04 updated board as of 04/08/23
    [CAN_toolboard_redesign.brd]
2023-08-08 Created New Schematic
    [CAN_toolboard_redesign.brd, PCB V2.1.dxf, TD Toolboard V2.brd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]
2023-08-08 Buck Converter Routing
    [FW_Toolboard1_v71(Eagle 9).brd, FW_Toolboard1_v71(Eagle 9).sch, TD Toolboard V2.brd]
2023-08-08 Buck Changed Finalised
    [TD Toolboard V2.brd]
2023-08-08 Added LDO Components
    [TD Toolboard V2.brd]
2023-08-08 Made Changes
    [TD Toolboard V2.brd]
2023-08-08 Routed most of the componenets to RP2040, Driver and GPIs remianing
    [FW_Toolboard1_v71(Eagle 9).brd, TD Toolboard V2.brd]
2023-08-09 TMC routed
    [TD Toolboard V2.brd, TD Toolboard V2.sch]
2023-08-09 Minor Changes
    [TD Toolboard V2.brd]
2023-08-09 Added holes, made board dimension layout, few other minor changes
    [TD Toolboard V2.brd]
2023-08-09 Placed other connectors and re arranged adxl345
    [TD Toolboard V2.brd, TD Toolboard V2.sch]
2023-08-09 Finished routing all components
    [TD Toolboard V2.brd, TD Toolboard V2.sch]
2023-08-09 Minor Changes for ground connectivity
    [TD Toolboard V2.brd]
2023-08-10 Fixed font sizes, added lables
    [TD Toolboard V2.brd, TD Toolboard V2.sch]
2023-08-11 Fixed errors, Passed DRC, added logos
    [TD Toolboard V2.brd]
2023-08-11 Added BOM and Centroid files
    [BOM TwinDragon.csv, placement.csv]
2023-08-14 Increased size of 24V polygon for heater
    [TD Toolboard V2.brd]
2023-10-13 Gerber, centroids, and other minor changes
    [placement.csv]
2023-10-18 minor changes in connector logic
    [TD Toolboard V2.brd, TD Toolboard V2.sch]
2023-10-20 Made the required changes - renamed toolboard to V3
    [BOM TwinDragon.csv, PCB V2.1.dxf, TD Toolboard V3.brd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]
2023-10-20 Revert "Made the required changes - renamed toolboard to V3"
    This reverts commit 7a8e9a42dd896dbf20b13a7ad3ff12e06b196980.
    [BOM TwinDragon.csv, PCB V2.1.dxf, TD Toolboard V2.brd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]
2023-10-20 routed the connections for the connectors whose logic were changed
    [TD Toolboard V2.brd, TD Toolboard V2.sch]
2023-10-25 updated fracktal logo with bmp
    [TD Toolboard V2.brd]
2023-12-21 Carriage Board added
    [Carriage Minifit PCB.brd, Carriage Minifit PCB.sch, TD Carriage MINIFIT board.dxf]
2023-12-21 Added Logo
    [Carriage Minifit PCB.brd, Carriage Minifit PCB.sch]
2023-12-23 Logo, Centroid, BOM, datasheet changes and addition
    [BOM TwinDragon.csv, Carriage Minifit PCB BOM.csv, Centroids - Top Layer.csv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]
2024-03-02 Updated Toolboard V2 and Carriage minifit boards specs
    Toolboard and Carriage minifit board design, gerber, BOMs, centroids and connector specifications have been updated here
    [Carriage Minifit PCB.brd, Carriage Minifit PCB.sch, TD ToolBoard V2 BOM_190124_AM.csv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]

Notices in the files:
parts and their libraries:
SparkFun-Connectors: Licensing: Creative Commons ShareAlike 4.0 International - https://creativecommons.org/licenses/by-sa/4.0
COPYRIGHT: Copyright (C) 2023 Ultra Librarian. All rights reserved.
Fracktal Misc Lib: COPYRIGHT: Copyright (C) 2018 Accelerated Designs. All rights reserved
